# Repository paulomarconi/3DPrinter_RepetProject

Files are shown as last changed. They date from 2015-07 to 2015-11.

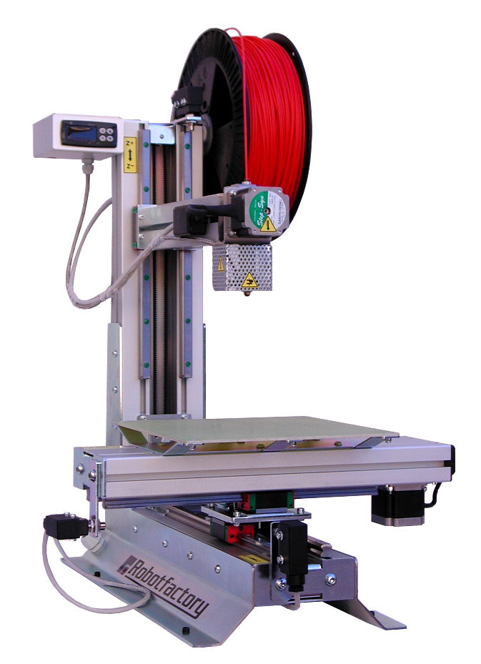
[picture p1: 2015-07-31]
software/3DPrinterWFA/3DPrinter/Resources/3D-ONE.jpg

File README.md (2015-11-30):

# Prototipo de Impresora 3D con el uso de botellas PET como material de impresión y adaptación de desecho electrónico (e-waste) para su construcción.

Basic 3D Printer prototype implementation with FDM technique by the application of plastic PET bottles as printing material replacing the traditional PLA/ABS, e-waste adaptation for the extruder and structure construction. Own electronic and Firmware-Software implementation for PID heating Joule Effect temperature control, Step by Step motors control, general operation and monitoring, Gcode descriptor and 3D positioning algorithms.

Implementación de un prototipo básico de Impresora 3D con la técnica FDM aplicando botellas plásticas PET desechables como material de impresión reemplazando el tradicional PLA/ABS, adaptación de desecho electrónico (e-waste) para la construcción del extrusor y la estructura. Implementación de diseño propio de electrónica y Firmware-Software para el control de temperatura PID por Efecto Joule, control de motores paso a paso (mPaP), operación y monitoreo general, algoritmos descriptor de Gcode y posicionamiento 3D.

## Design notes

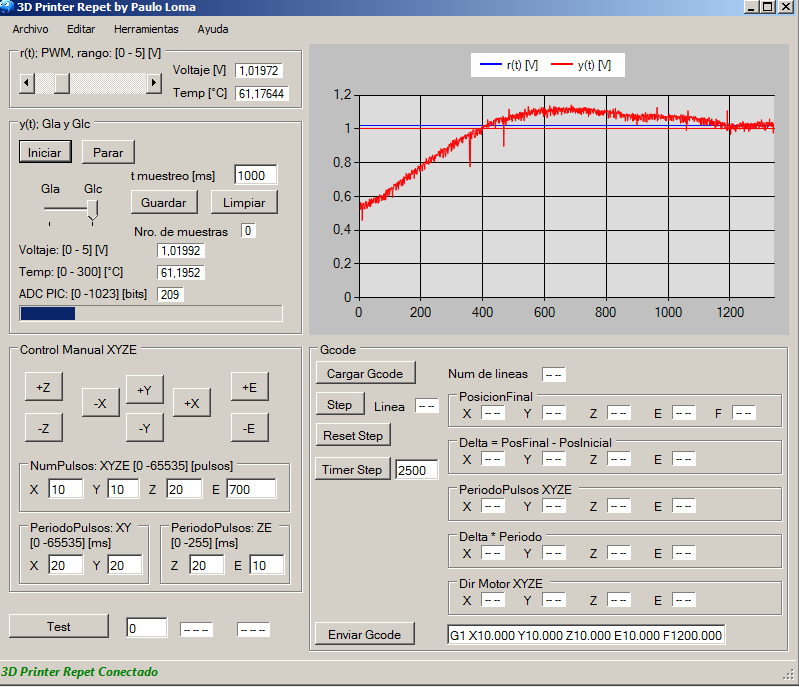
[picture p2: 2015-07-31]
analisis/datosRecolectados/PID_tm1000ms_19V_0a1V_3kHz_a.png

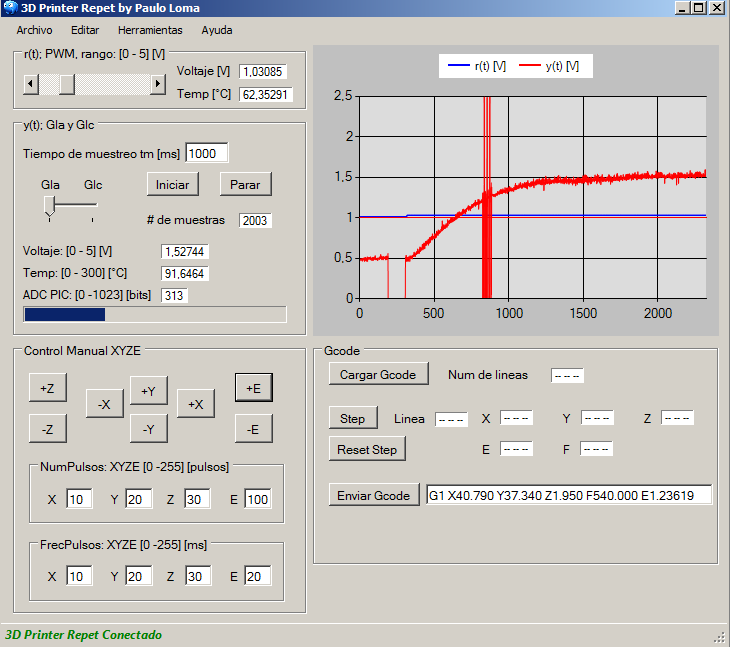
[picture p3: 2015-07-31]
analisis/datosRecolectados/Gp_tm1000ms_19V_0a1V_3kHz.png

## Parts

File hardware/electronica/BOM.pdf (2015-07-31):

## Bill Of Materials For Repet 3D Printer

Design Title | Repet 3D Printer
Author | Paulo Loma

### Revision

Design Created | viernes, 12 de julio de 2013
Design Last Modified lunes, 30 de junio de 2014

### Total Parts In Design 141

1 Integrated Circuits

Quantity | References | Value
1 | U1 | LM35
Sub-totals:

140 Miscellaneous

Quantity | References | Value
2 | BOOT,RESET
4 | CE1,CX1,CY1,CZ1 | 3.3nF
8 | CE2,CPIC1,CPIC2,CT1,CX2,CX3,CY2,CZ2 | 100nF
2 | CPIC3,CPIC4 | 15pF
1 | CPIC5 | 220nF
4 | CT2,CT3,CT4,CT5 | 10nF
1 | CT6 | 10uF
1 | CX4 | 470uF
12 | DE1,DE2,DE3,DE4,DY1,DY2,DY3,DY4,DZ1,DZ2,DZ3,DZ4 | DIODE-ZEN
2 | DPIC1,DPIC2 | 1N4007
1 | DSW1 | DIPSW_1
8 | DX1,DX2,DX3,DX4,DX5,DX6,DX7,DX8 | DIODE
3 | GLALGLC,LED_USB,PULSOS | LED-GREEN
6 | JE1,JTCK1,JX1,JX2,JY1,JZ1 | SIL-100-04
3 | JE2,JY2,JZ2 | SIL-100-06
2 | JEX1,JPIC | SIL-100-02
3 | JEX2,JTCK2,JTCK3 | TBLOCK-I2
12 | QE1,QE2,QE3,QE4,QY1,QY2,QY3,QY4,QZ1,QZ2,QZ3,QZ4 | TIP122
1 | QEX | IRL3803
4 | RE1,RX1,RY1,RZ1 | 22k
6 | RE2,RE3,RX2,RX3,RZ2,RZ3 | 0.5R
21 | RE4,RE6,RE7,RE8,RE9,RPIC4,RT5,RT6,RT7,RT8,RX4,RY4,RY6,RY7,RY8,RY9,RZ4,RZ6,RZ7,RZ8,RZ9 1k
5 | RE5,RPIC3,RPIC5,RX5,RY5 | 10k
1 | REX1 | 10R
3 | REX2,RPIC6,RPIC8 | 100k
1 | RGT | 120
3 | RPIC1,RPIC2,RPIC7 | 220R
2 | RT1,RT3 | 100
2 | RT2,RT4 | 330
1 | RT9 | 15k
1 | RZ5 | 10K
4 | UE1,UX1,UY1,UZ1 | L297
2 | UE2,UZ2 | 74HC08
1 | UPIC | PIC18F4550
1 | USB | USBCONN
2 | UT2,UT4 | OP07
1 | UT3 | AD620
1 | UT5 | TL081
1 | UX2 | L298
1 | XPIC | CRYSTAL
Sub-totals:

Totals:

miércoles, 02 de julio de 2014 05:32:06 p.m.

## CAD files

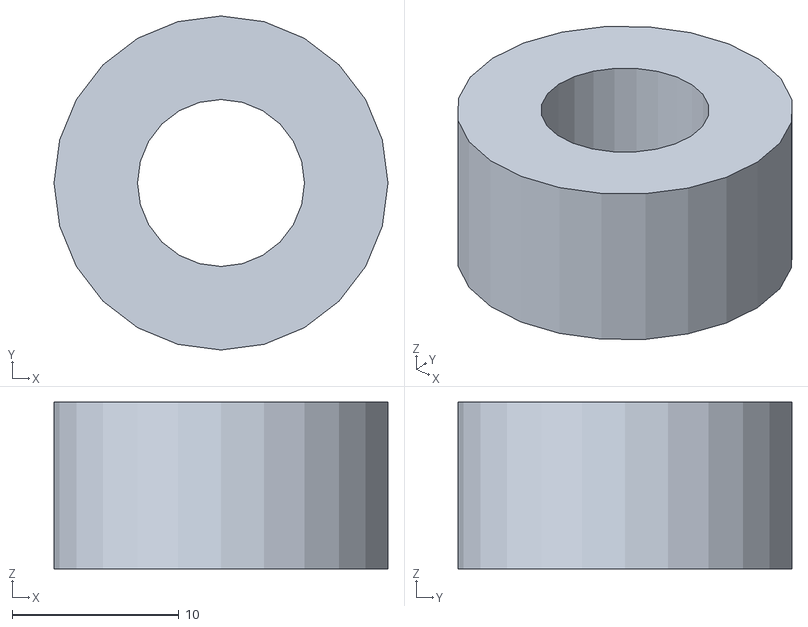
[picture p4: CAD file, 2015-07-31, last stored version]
analisis/testsModels/test2.stl
20.0 x 20.0 x 10.0

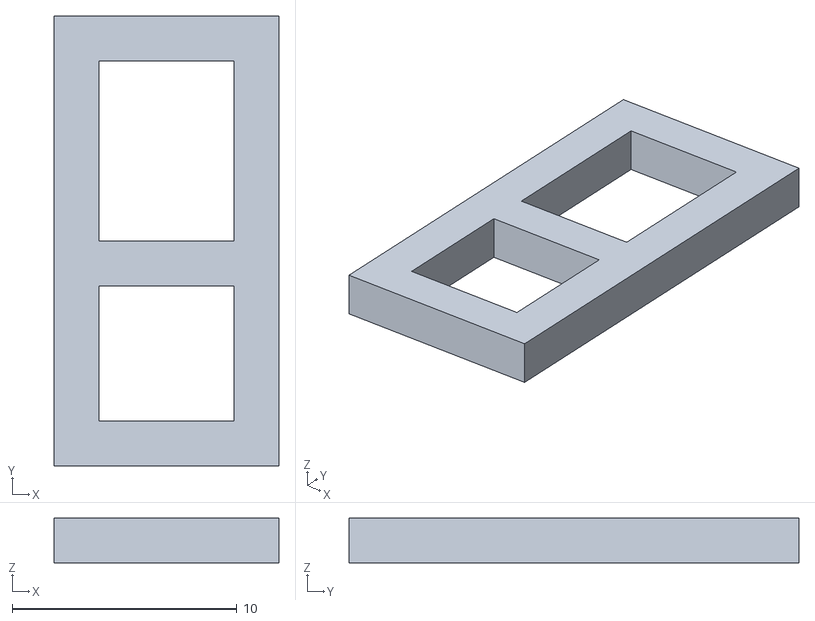
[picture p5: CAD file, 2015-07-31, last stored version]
analisis/testsModels/B.stl
10.0 x 20.0 x 2.00

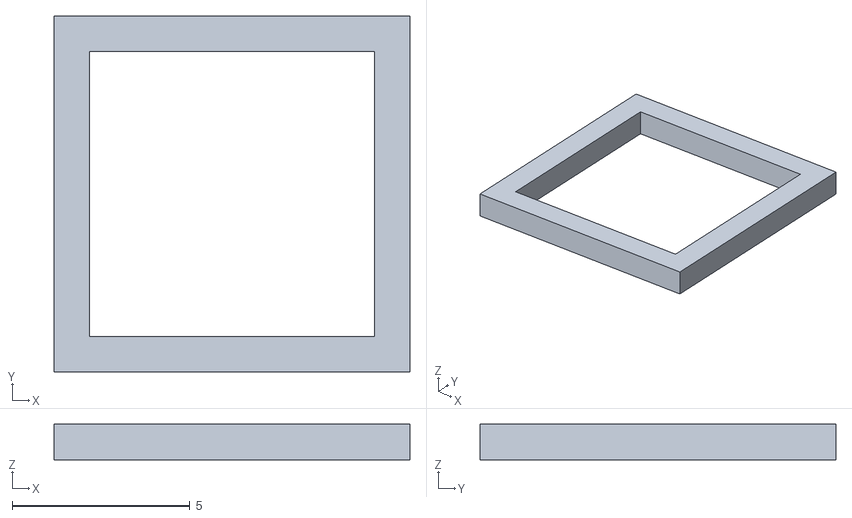
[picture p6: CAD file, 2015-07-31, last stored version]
analisis/testsModels/test3.stl
10.0 x 10.0 x 1.00

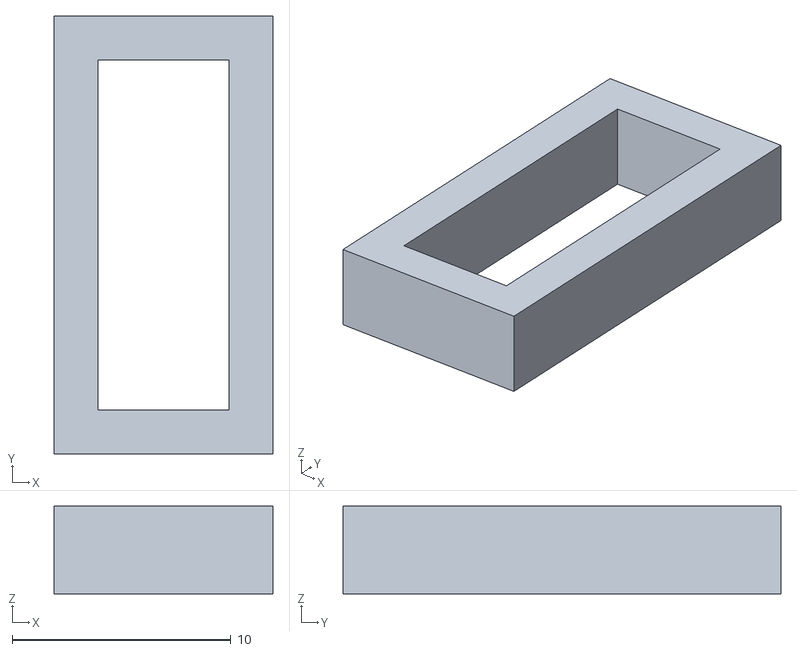
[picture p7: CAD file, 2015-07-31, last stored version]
analisis/testsModels/rectangulo.stl
10.0 x 20.0 x 4.00

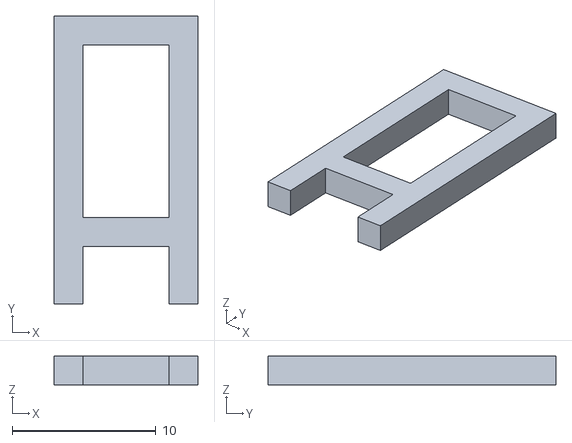
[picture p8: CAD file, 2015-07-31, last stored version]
analisis/testsModels/A.stl
10.0 x 20.0 x 2.00

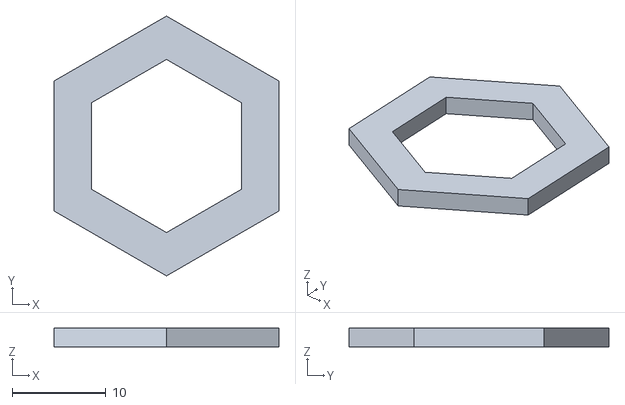
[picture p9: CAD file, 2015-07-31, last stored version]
analisis/testsModels/hexagono.stl
24.0 x 27.7 x 2.00

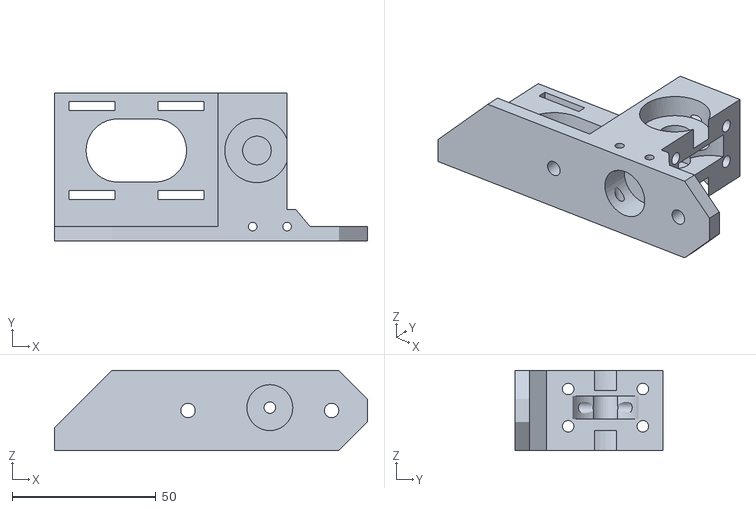
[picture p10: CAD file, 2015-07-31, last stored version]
analisis/testsModels/M8_Extruder_Block_3.stl
109.0 x 51.5 x 28.0

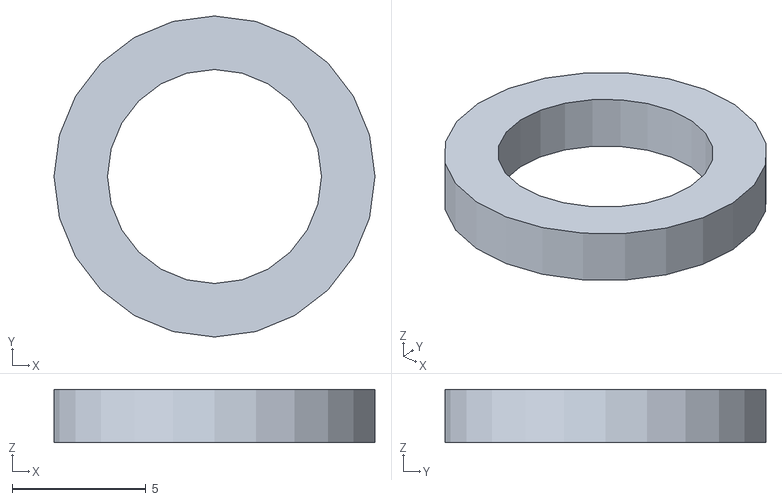
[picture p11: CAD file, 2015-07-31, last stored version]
analisis/testsModels/circulo.stl
12.0 x 12.0 x 2.00

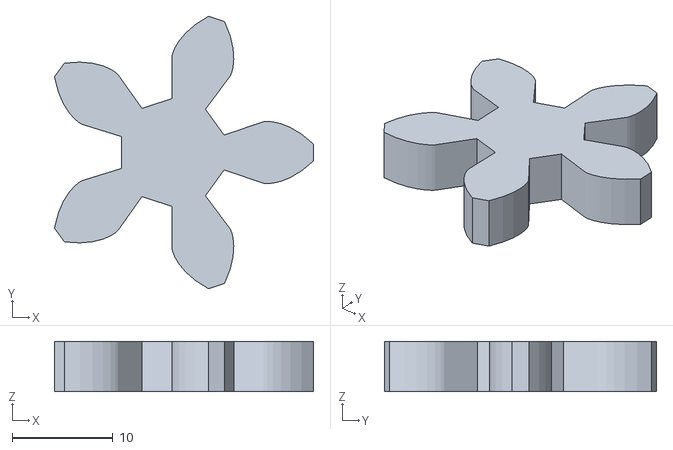
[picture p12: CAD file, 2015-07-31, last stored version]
analisis/testsModels/engranaje.stl
25.8 x 27.1 x 5.00

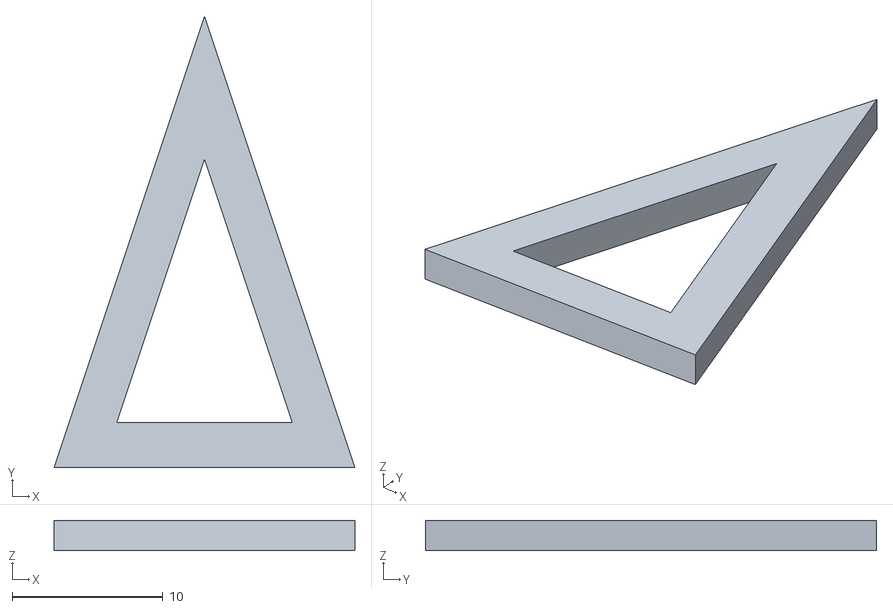
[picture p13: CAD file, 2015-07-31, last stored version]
analisis/testsModels/triangulo.stl
20.0 x 30.0 x 2.00

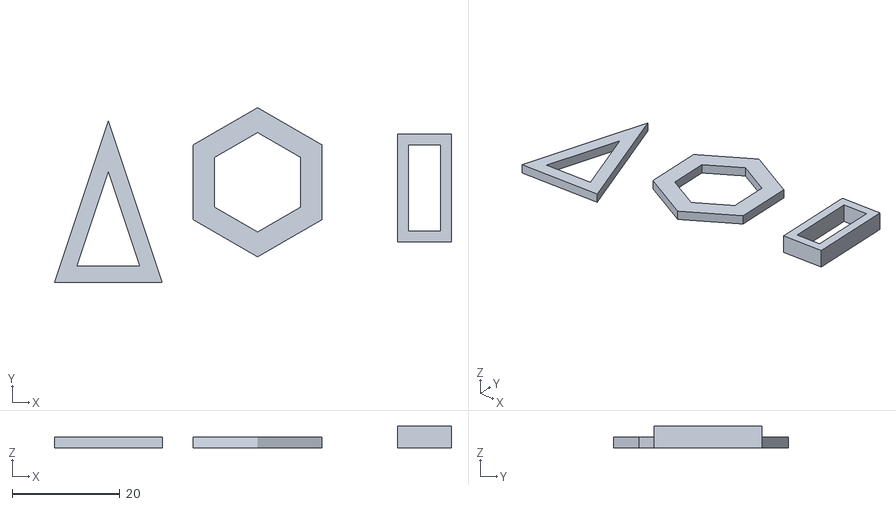
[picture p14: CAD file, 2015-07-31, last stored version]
analisis/testsModels/test1.stl
73.7 x 32.4 x 4.00

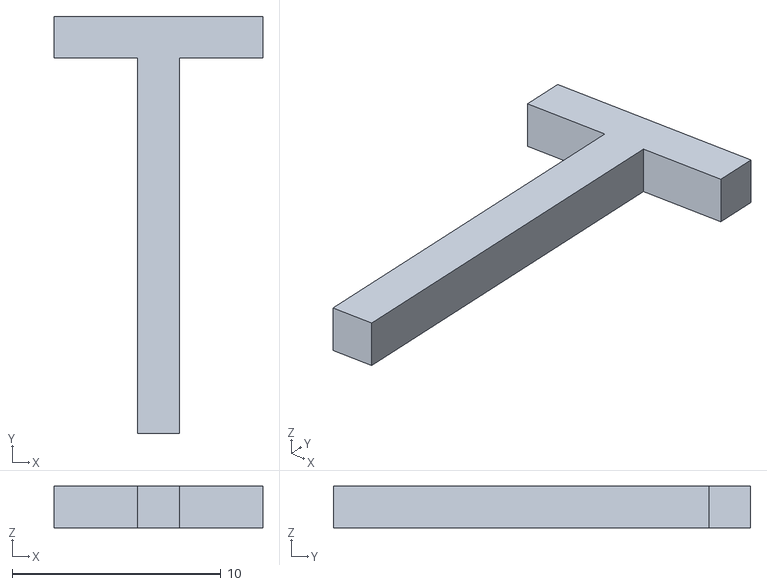
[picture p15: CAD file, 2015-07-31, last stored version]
analisis/testsModels/T.stl
10.0 x 20.0 x 2.00

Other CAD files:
hardware/mecanica/desarrollo tolva.dwg
analisis/testsModels/paralepido.stl
analisis/testsModels/test1.skp

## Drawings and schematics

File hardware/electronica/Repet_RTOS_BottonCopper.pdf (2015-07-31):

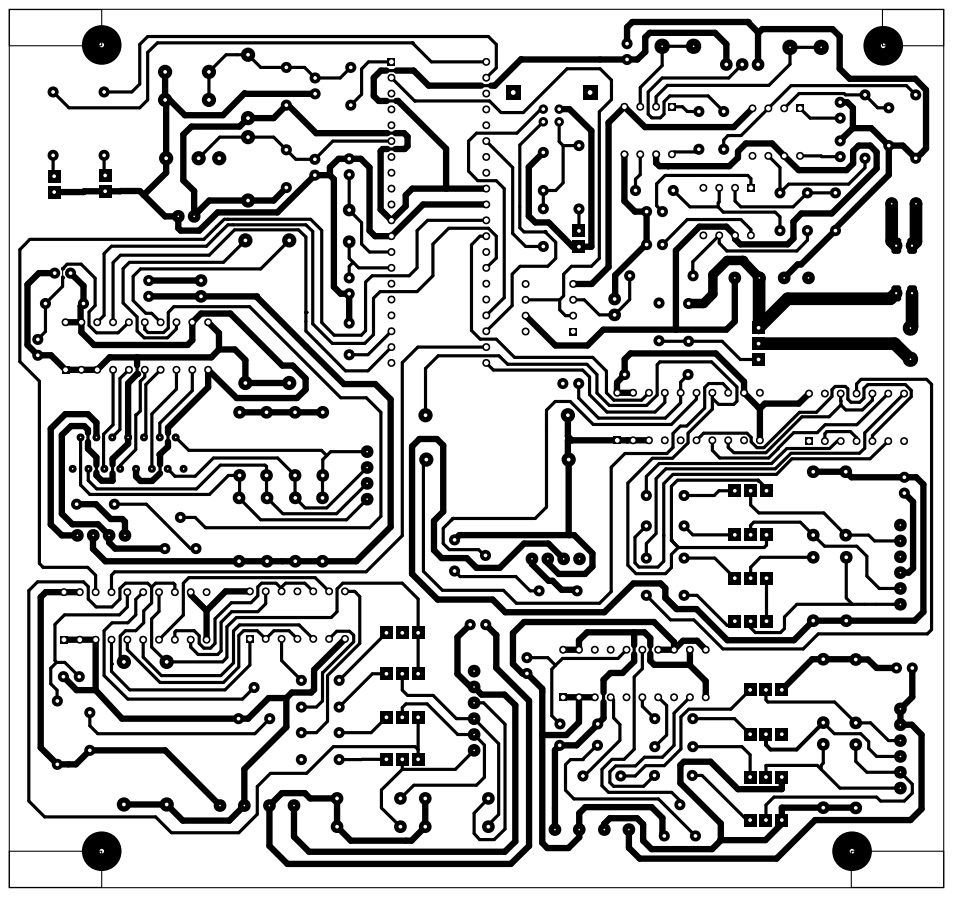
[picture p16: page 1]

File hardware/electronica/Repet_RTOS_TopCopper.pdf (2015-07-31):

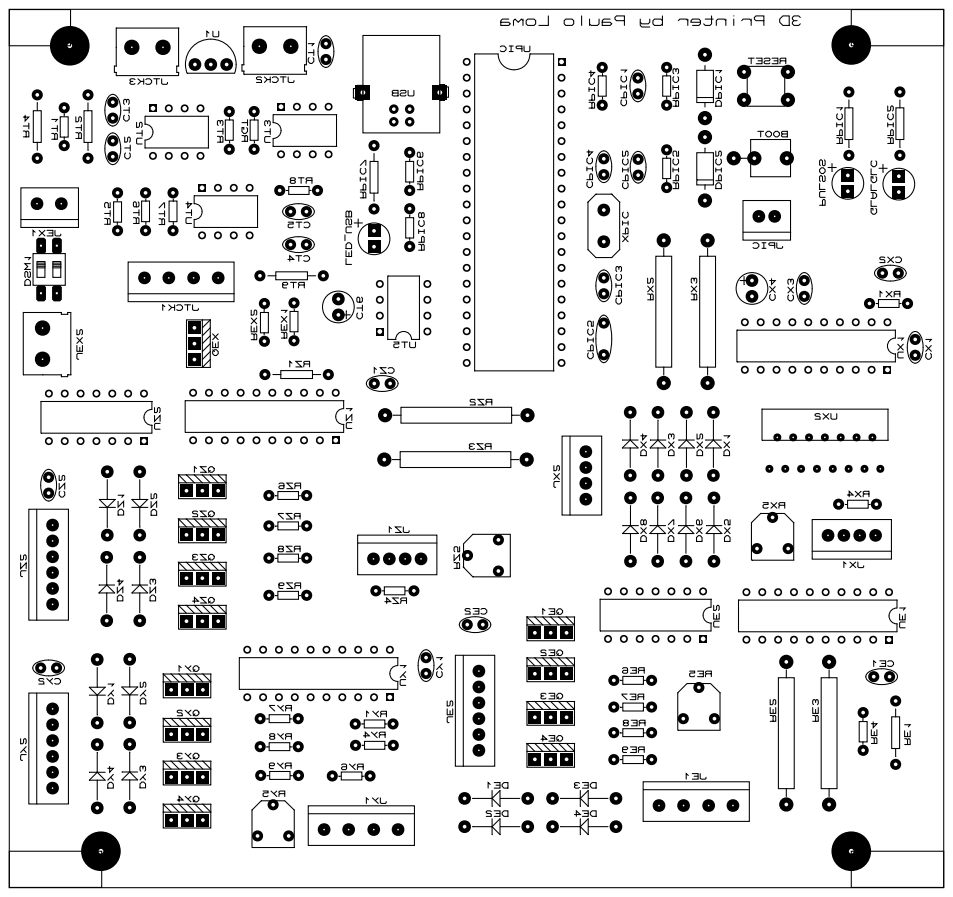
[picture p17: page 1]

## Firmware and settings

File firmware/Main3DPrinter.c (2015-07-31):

//--- config: PIC ------------------------------------------------------------
#include <18F4550.h>
#device adc=10
#fuses HSPLL,MCLR,NOWDT,NOPROTECT,NOLVP,NODEBUG,USBDIV,PLL5,CPUDIV1,VREGEN 
#use delay(crystal=20MHz, clock=48MHz) 

//cabecera necesaria para trabajar con el Bootloader "ex_usb_bootloader.c"
#include "usb_bootloader.h"

//--- config: USB bulkmode ---------------------------------------------------
#define USB_HID_DEVICE     FALSE
#define USB_EP1_TX_ENABLE  USB_ENABLE_BULK  //turn on EP1(EndPoint1) 
                                            //for IN bulk/interrupt transfers
#define USB_EP1_RX_ENABLE  USB_ENABLE_BULK  //turn on EP1(EndPoint1) 
                                            //for OUT bulk/interrupt transfers
#define USB_EP1_TX_SIZE    3   //size to allocate for the tx endpoint 1 buffer
#define USB_EP1_RX_SIZE    20  //size to allocate for the rx endpoint 1 buffer

#include <pic18_usb.h>        //Microchip PIC18Fxx5x Hardware layer 
                              //for CCS's PIC USB driver
#include "usb_descriptor.h"   //Configuracion del USB y los descriptores 
                              //para este dispositivo
#include <usb.c>  //handles usb setup tokens and get descriptor reports

#include <osa.h>  //OSA RTOS

//--- config: Directivas I/O -------------------------------------------------
#use standard_io(A)
#use standard_io(B)
#use standard_io(C)
#use standard_io(D)

//--- def: variables Tarea USB -----------------------------------------------
unsigned int8  RecibirByte[20];   //vector [0;19]=20 vectores x 1Byte                
unsigned int8  EnviarByte[3];     //vector [0;2]=3 vectores x 1Byte

//--- def: variables Tareas mPaP ---------------------------------------------
unsigned int16 numPulsosX,numPulsosY,numPulsosZ,numPulsosE;   
unsigned int16 periodoPulsosX,periodoPulsosY;
unsigned int8 periodoPulsosZ,periodoPulsosE;
unsigned int8 dirMotorX,dirMotorY,dirMotorZ,dirMotorE;    
#define dirX    PIN_D0
#define dirY    PIN_D1
#define dirZ    PIN_D2
#define dirE    PIN_D3
#define clockX  PIN_D4 
#define clockY  PIN_D5
#define clockZ  PIN_D6
#define clockE  PIN_D7

//--- def: variables para funciones; ADC PIC, Gla, GlcPID --------------------
unsigned int8 GlaoGlc;
unsigned int16 valorR,valorY,valorYusb,control;
float Kp,Kd,Ki,Kpz,Kiz,Kdz,T;    //Constantes PID  
float r,y,u,e,e1,p,i,i1,d,d1;    //Variables PID
unsigned int16 max,min;          //Variables anti-windup 

//--- def: Funciones Genericas -----------------------------------------------
void Inicio (void);
void ADC(void);

//--- def: Tareas OSA --------------------------------------------------------
void USB(void);
void Gla(void);
void Glc_PIDdiscreto(void);
void MotorX(void);
void MotorY(void);
void MotorZ(void);
void MotorE(void);

//****************************************************************************
//**** main
//****************************************************************************
void main(void){
   
   Inicio();
   
   OS_Init();              // Init OS
   OS_Task_Define(USB);    // Define tasks.
   OS_Task_Define(Gla); 
   OS_Task_Define(Glc_PIDdiscreto);         
   OS_Task_Define(MotorX);
   OS_Task_Define(MotorY);
   OS_Task_Define(MotorZ);        
   OS_Task_Define(MotorE);
   
   // Create tasks. // if 0 = no priorities 
   OS_Task_Create(0, USB);    
   OS_Task_Create(0, Gla);
   OS_Task_Create(0, Glc_PIDdiscreto);      
   OS_Task_Create(0, MotorX);  
   OS_Task_Create(0, MotorY);
   OS_Task_Create(0, MotorZ);  
   OS_Task_Create(0, MotorE);
   
   // Create tasks, Task priority. Allowed values from 0(highest) to 7(lowest)
   /*OS_Task_Create(0, USB);    
   OS_Task_Create(7, Gla);
   OS_Task_Create(1, Glc_PIDdiscreto);      
   OS_Task_Create(2, MotorX);  
   OS_Task_Create(2, MotorY);
   OS_Task_Create(2, MotorZ);  
   OS_Task_Create(2, MotorE);
   
   OS_Bsem_Set(BS_GLAGLC_FREE);*/
   
   OS_EI();                // Enable interrupts
   OS_Run();               // Running scheduler
}

//**** Funciones genericas ***************************************************
void Inicio(void){ 
   //--- ini: mPaP -----------------------------------------------------------
   numPulsosX=numPulsosY=numPulsosZ=numPulsosE=0;
   periodoPulsosX=periodoPulsosY=periodoPulsosZ=periodoPulsosE=0;
   //--- ini: PID ------------------------------------------------------------
   min=0.0; max=1023 ; //valor Anti-windup    
   i1=0;e1=0;d1=0;   
   Kd=8; Kp=8; Ki=0.02915;
   T=5;       //Tiempo de muestreo  tr/6 < T < tr/20
   Kpz=Kp; Kiz=Ki*T/2; Kdz=Kd/T;
   
   //--- ini: CCP ---------------------------------------------------------
   //--- Pre=16 PR2=249 Pos=1, PWMF=3kHz,PWMT=300us con Fosc(clock)=48MHz
   setup_timer_2(T2_DIV_BY_16,249,1); 
   setup_ccp1(ccp_pwm);               //Configurar modulo CCP1 en modo PWM
   set_pwm1_duty(0);  
   
   //--- ini: ADC ---------------------------------------------------------  
   setup_adc_ports(AN0|VSS_VDD );     
   setup_adc(ADC_CLOCK_INTERNAL); 
   //setup_adc(ADC_CLOCK_DIV_8); //respetar el Tad>1.6us 
                                 //Tad=8/Fosc=8/20Mhz=400ns
   set_adc_channel(0);           //Seleccionar Canal(0)=AN0=A0 para ADC
   
   //--- ini: TIMER0 for OS_Timer() ---------------------------------------                                  
   setup_timer_0(RTCC_INTERNAL|RTCC_DIV_1);  //config Timer0, Pre=1=RTCC_DIV_1
   //set_timer0(0xF63B);   //carga del Timer0, clock=20MHz, Fout=1kHz=0xF63B
   set_timer0(0xE88F);     //carga del Timer0, clock=48MHz, Fout=1kHz=0xE88F
   
   //--- ini: Interrupts --------------------------------------------------
   //enable_interrupts(GLOBAL);
   enable_interrupts(INT_TIMER0);            //habilita interrupcion Timer0
   //enable_interrupts(INT_TIMER2);
   
   //--- ini: USB ------------------------------------------------------------
   usb_init();                   //inicializamos el USB
   usb_task();                   //habilita periferico usb e interrupciones
   usb_wait_for_enumeration();   //esperamos hasta que el PicUSB 
                                 //sea configurado por el host
   delay_ms(50);   
}

void ADC(void){
   valorYusb=read_adc();
   //delay_us(1); //Tacq minimo de carga 
                  //del capacitor(sample&hold)=8/Fosc=8/20MHz=400ns=0.4us
                  
   //-- El ADC es de 10 bits y puedo enviar solo 8, asi que separo
   //-- la variable en 2 bytes "EnviarByte[0] y EnviarByte[1]", 
   //-- luego se arma en C# (ver notas)
   EnviarByte[0]=valorYusb >> 8;   //desplazamiento de 8bits a la derecha
   EnviarByte[1]=valorYusb & 0xFF; //a & b = AND binario
}

//**** Tareas OSA ***********************************************************
#INT_TIMER0
void timer0_isr(void){  
   OS_Timer();
   set_timer0(0xE88F);    //se recarga el Timer0   
}   

void USB(void){
   for(;;){
      if(usb_enumerated()){   //True si el USB ha sido enumerado.      
         if(usb_kbhit(1)){    //(endpoint=1 EP1)= TRUE si el EP1 tiene datos 
                              //en su buffer de recepcion.
            
            //-- (endpoint,ptr,max)=Reads up to max bytes from
            //-- the specified endpoint buffer and saves it to the pointer ptr
            //-- Returns the number of bytes saved to ptr
            usb_get_packet(1,RecibirByte,20);
                                             
            //-- revisa en orden logico el contenido de 
            //-- RecibirByte[0],[1],[2],[3],[4]....
            //-- *2, OSA usa el doble de pulsos
            numPulsosX     = (RecibirByte[0]*256+RecibirByte[1])*2;  
            numPulsosY     = (RecibirByte[2]*256+RecibirByte[3])*2;
            numPulsosZ     = (RecibirByte[4]*256+RecibirByte[5])*2;
            numPulsosE     = (RecibirByte[6]*256+RecibirByte[7])*2;
            periodoPulsosX = (RecibirByte[8]*256+RecibirByte[9]);
            periodoPulsosY = (RecibirByte[10]*256+RecibirByte[11]);
            periodoPulsosZ = RecibirByte[12];
            periodoPulsosE = RecibirByte[13];
            dirMotorX      = RecibirByte[14];
            dirMotorY      = RecibirByte[15];
            dirMotorZ      = RecibirByte[16];
            dirMotorE      = RecibirByte[17];
            GlaoGlc        = RecibirByte[18];
            valorR         = RecibirByte[19];  
         }         
         //-- reviso en orden logico EnviarByte[0],[1] y envio por usb               
         ADC();    //esta funcion contiene los valores de EnviarByte[0;1]
         if( (numPulsosX || numPulsosY || numPulsosZ || numPulsosE) != 0) {EnviarByte[2]=1; output_high(PIN_B6);}
         else {EnviarByte[2]=0; output_low(PIN_B6);}
         
         //-- (endpoint,data,len,tgl)=Places the packet of data
         //-- into the specified endpoint buffer.
         //-- Returns TRUE if success, FALSE if the buffer 
         //-- is still full with the last packet.
         usb_put_packet(1,EnviarByte,3,USB_DTS_TOGGLE);                                                                     
      }      
      OS_Delay(10); 
      OS_Yield();
   }
}

void Gla(void){
   for(;;){      
      OS_Wait(GlaoGlc==3);
      //OS_Bsem_Wait(BS_GLAGLC_FREE); 
      output_toggle(PIN_B7);
      
      //-- 1023/255=4.012, necesita adaptarse al mismo rango 
      //-- porque el valorR que llega desde el GUI tiene max=255
      r=(float)(valorR*4.012);   
      control=(unsigned int16)r;
      set_pwm1_duty(control);
      
      OS_Delay(1000);
      //OS_Bsem_Set(BS_GLAGLC_FREE); 
      OS_Yield();            
   }
}

void Glc_PIDdiscreto(void){
   for(;;){  
      OS_Wait(GlaoGlc==2); //2
      //OS_Bsem_Wait(BS_GLAGLC_FREE); 
      output_toggle(PIN_B7);
    
      valorY=read_adc(ADC_READ_ONLY);
      //-- debido al ADC 10bits, la conversion se realiza con 10bits, 
      //-- entonces valorY tiene rango de 0 a 1023
      y=(float)valorY;
      //-- 1023/255=4.012, necesita adaptarse al mismo rango 
      //-- porque el valorR que llega desde el GUI tiene max=255
      r=(float)(valorR*4.012);
      //----------------------------------------------------------------------
      //-- Calculo PID por metodo tustin para termino integral 
      //-- y metodo de diferencias hacia atras para termino derivativo
      //-- Sea e(kT)=e; e(kT-T)=e1
      e=r-y;               
      //Sea p(kT)=p; i(kT)=i; i(kT-T)=i1; d(kT)=d
      p=Kpz*e;        
      //i=i1+Kiz*e;    //diferencia hacia atras
      i=i1+Kiz*(e+e1);  //tustin
      d=Kdz*(e-e1);  //diferencia hacia atras
      
      //Sea u(kT)=u
      u=p+i+d;   
       
      //-- Anti-windup solo al termino integral para evitar que se infle
      //-- y se haga muy grande si la accion de control se satura, por tanto
      //-- es necesario impedir que cambie i
      //if((u>max) | (u<min)) {i=i-Ki*T*e;}      //diferencia hacia atras
      //if((u>max) | (u<min)) i=i-Kiz*(e+e1);     //tustin
      if(u>max)u=max;
      if(u<min)u=min;
                    
      //-- realizar la conversion final
      control=(unsigned int16)u;
      set_pwm1_duty(control);           
      e1=e;
      i1=i;
      
      OS_Delay(5000);
      //OS_Bsem_Set(BS_GLAGLC_FREE);
      OS_Yield();
   }
}



void MotorX(void){
   for(;;){
      OS_Wait(numPulsosX>0);
      if(dirMotorX==64)    output_high(dirX);
      if(dirMotorX==128)   output_low(dirX);
      if(--numPulsosX!=0)  output_toggle(clockX);  
      else  output_low(clockX);     
      OS_Delay(periodoPulsosX);
      OS_Yield();
   }
}

void MotorY(void){
   for(;;){
      OS_Wait(numPulsosY>0);
      if(dirMotorY==32)    output_high(dirY);
      if(dirMotorY==16)    output_low(dirY);
      if(--numPulsosY!=0)  output_toggle(clockY);  
      else  output_low(clockY);
      OS_Delay(periodoPulsosY);
      OS_Yield();
   }
}

void MotorZ(void){
   for(;;){
      OS_Wait(numPulsosZ>0);
      if(dirMotorZ==8)     output_high(dirZ);
      if(dirMotorZ==4)     output_low(dirZ);
      if(--numPulsosZ!=0)  output_toggle(clockZ);  
      else  output_low(clockZ);     
      OS_Delay(periodoPulsosZ);
      OS_Yield();
   }
}

void MotorE(void){
   for(;;){
      OS_Wait(numPulsosE>0);
      if(dirMotorE==1)     output_high(dirE);
      if(dirMotorE==2)     output_low(dirE);
      if(--numPulsosE!=0)  output_toggle(clockE);  
      else  output_low(clockE);     
      OS_Delay(periodoPulsosE);
      OS_Yield();
   }
}
